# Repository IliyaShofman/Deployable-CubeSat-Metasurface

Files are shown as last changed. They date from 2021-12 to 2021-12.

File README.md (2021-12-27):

## What is this?
This is my research project during my internship at the Reconfigurable Antenna Laboratory in the summer of 2020. I've summarized the 4-month project in the "Supper Report.PDF" file. 

*The goal of this project is to develop a mechanism which would stow and deploy flat, thin Metasurface panels that cover a large area from a small-volume nanosatellite. Novel prototypes, testing setups and measuring methods have been developed and built to validate the design in laboratory settings. This research, sponsored by Thales Alenia Space, will enable the demonstration of technological matureness for deployed meta-surface antenna systems for emerging 5G and IoT space communication applications.*

The SOLIDWORKS model of the concept is sotred in this repository. 

## Design Concept

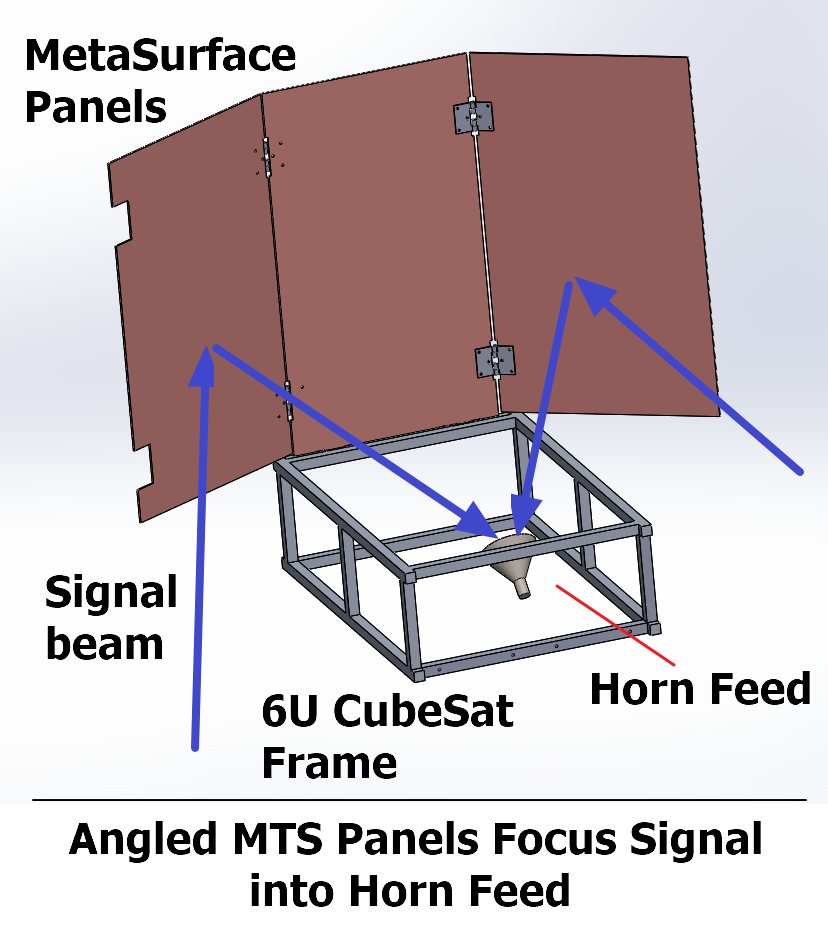
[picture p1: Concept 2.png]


## Deployment Animation

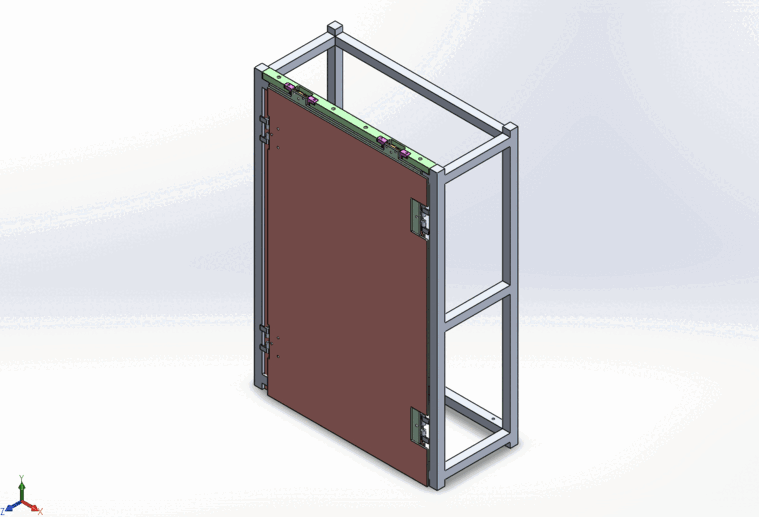
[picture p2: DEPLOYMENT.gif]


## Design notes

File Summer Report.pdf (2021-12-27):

## Deployable Metasurface Antennas for CubeSats

In this report I will summarize the work I have done during the 2020 FYSRF with Dr. Sean V. Hum on Deployable Metasurface Antennas. The goal of this project is to develop a mechanism which would stow and deploy flat, thin Metasurface panels that cover a large area from a small-volume nanosatellite. Novel prototypes, testing setups and measuring methods have been developed and built to validate the design in laboratory settings. This research, sponsored by Thales Alenia Space, will enable the demonstration of technological matureness for deployed meta-surface antenna systems for emerging 5G and IoT space communication applications.

This report will present my contributions to the research project in chronological order, organized by month. At the end, I will reflect on key lessons I learned during the work term.

### May – Understanding the Problem and Conceptual Design:

After being introduced to the research problem, I was encouraged to research deployable space structures in the research literature, which covers a wide range of topics from origami-deploying antennas to inflatable space station modules. Although we had limited input from the stakeholder, we anticipated that a CubeSat-sized satellite would be most appropriate for their mission requirements. Therefore, I focused on learning about CubeSats and deployable solar panel systems. This allowed me to explore functionally similar reference designs and understand the physical constraints on the desired solution.

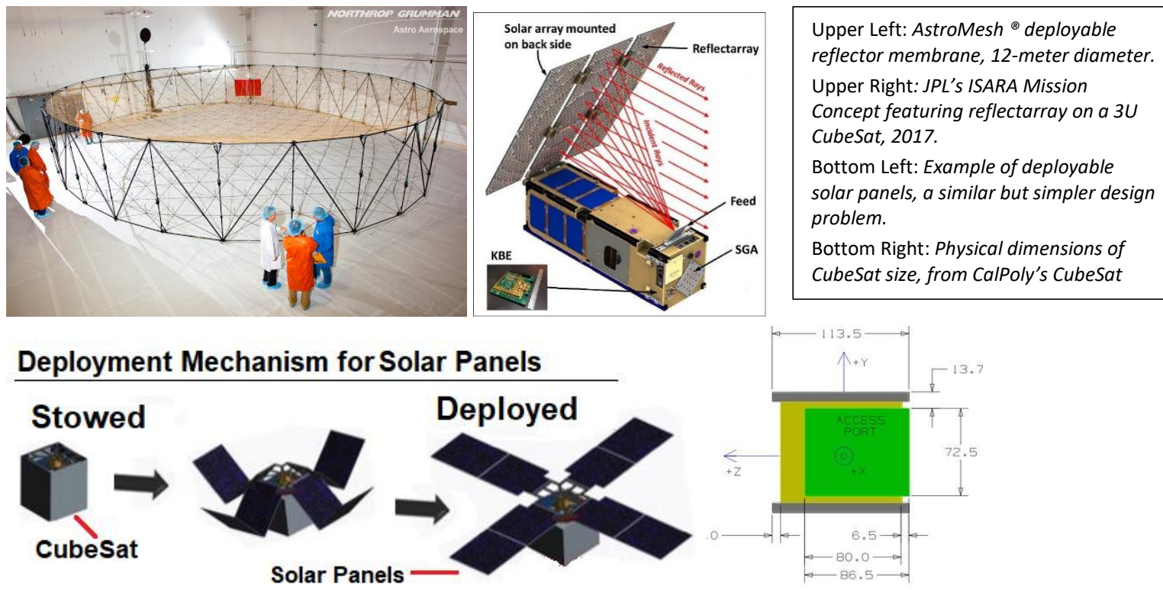
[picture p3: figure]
Upper Left: AstroMesh ® deployable reflector membrane, 12-meter diameter. Upper Right: JPL’s ISARA Mission Concept featuring reflectarray on a 3U CubeSat, 2017. Bottom Left: Example of deployable; problem. Bottom Right: Physical dimensions of CubeSat size, from CalPoly’s CubeSat

At this stage, I began to brainstorm various designs and mechanisms to accomplish the following objectives:

- Stow the deployable Metasurface panels within the space constraints of a 6U CubeSat.
- Reliably release the Metasurface panels upon command.
- Physically move panels into operational configuration, without failure and risk to the satellite.
- Accurately lock the panels in their final positions that provide the best gain and bandwidth.

solar panels, a similar but simpler design

The design of a deployable space system is challenging because a wealth of precautions against must be taken to ensure the design will not fail in space. The concerns over cold-welding, thermal cycling, vacuum out-gassing, and solar radiation are reflected in deliberate design and material choices that differentiate the solution from, say, a kitchen cabinet. To simplify the design, we decided to create a design that can be mounted externally to a 6U CubeSat. While this significantly limits design freedom, we thought it was strategically better to demonstrate Metasurface on a simple, failproof deployment system before testing complex designs.

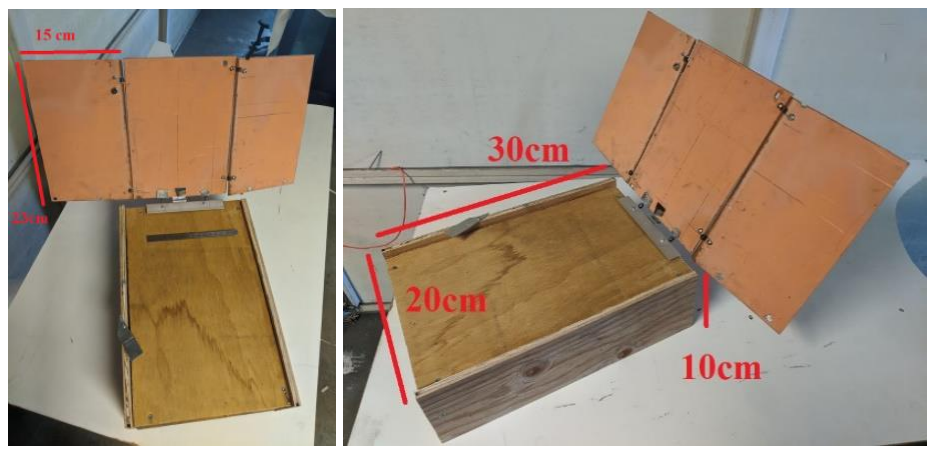
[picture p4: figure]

### June – Initial Prototyping:

After making a conceptual model (pictured above) of the deployment system, I investigated alternatives to individual elements and built basic physical prototypes for each. Options like micro-motors, flexure and SMA joints were eliminated due to higher design complexity; A combination of magnetic clips and blocking plate was chosen for their simplicity; and the Nichrome wire- fishing line solution was chosen for its success in previous space missions.

Hold and Release | Guided Deployment | Final Blocking
Mechanical Latch/ Hook Solenoid and/or electromagnet Nichrome Burn Wire and Fishing Line | Torsional Springs & Hinges Flexure joints Shape Memory Alloy joints Micro-Motors | Spring-loaded Latch Simple block-plate Magnetic Clip Tensioning Cables

Having finalized the conceptual design, I modeled the system in SolidWorks and designed mechanical parts that comprise the system. Custom-built hinges that conform to space constraints and house the torsional springs were designed, along with their mechanical interface with a standard 6U CubeSat frame. The four picture below show the deployment sequence, while the 6 pictures below show detailed closeups of critical design elements.

Conceptual Prototype: 3 panels (folded together) rotate away from the larger face of the 6U CubeSat. Then, two side panels rotate 180 degrees from the middle panel, powered by torsional springs. Alternatives to torsional springs were investigated in June.

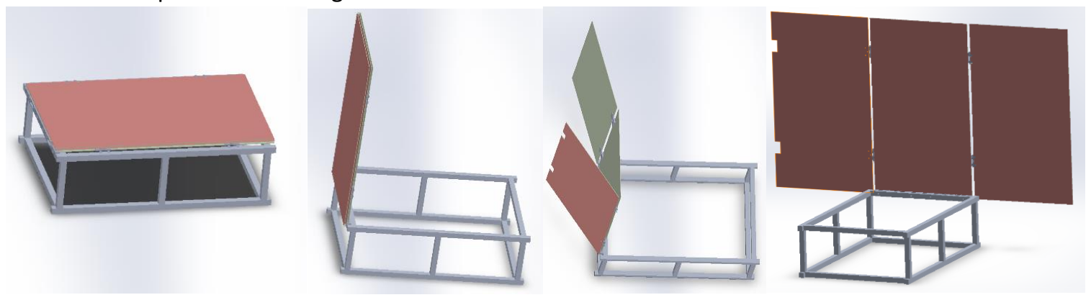
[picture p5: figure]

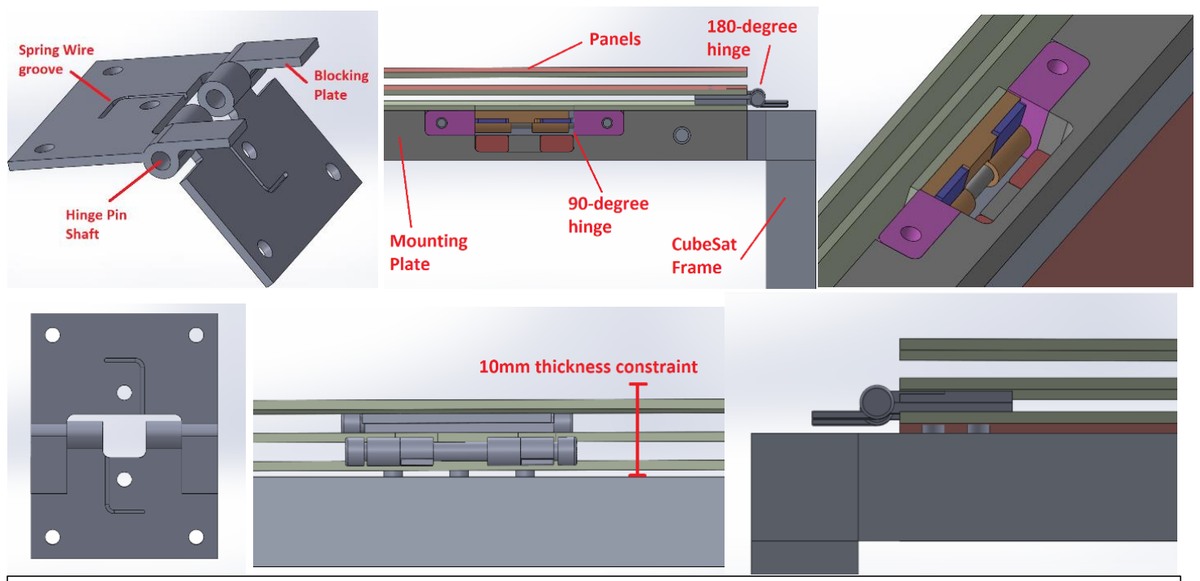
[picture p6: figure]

At this level of design, the primary concerns consisted of dimensions and tolerances for each feature such as a hole, material thickness, length, etc. After ensuring that the parts were realistically sized with an additional safety margin, I contacted several CNC fabrication shops for quotations on part manufacturing costs.

### June - Design of Testing Setup:

Meanwhile, thought was given on how to test the deployment mechanism in a laboratory before launching it into space. It is critical to know if and how the panels may fail to unfold, which may include friction in the joints, manufacturing defects, and material failures. As an extension, the electromagnetic characteristics of the Metasurface may be measured for consistency and accuracy to ensure the antenna will function as expected in space.

To test the deployment mechanism, it is necessary to emulate the space environment – especially microgravity. When the panels deploy on earth, the springs must be made strong enough to fight against gravity forces during the unfolding process. In space, however, these springs will be too strong and could fling the panels too rapidly, which will make the satellite tumble out of control. Thus, a setup that allows for closer-to-realistic mechanical performance testing of the prototype is necessary.

A large cage out of PVC tubing and connectors was devised. Constant force springs and nylon fishing line cables will be used to suspend the CubeSat frame and the deployable panels, thereby bearing the gravitational forces on the prototype. As the panel deploys, low-friction rails will guide the movement of the suspension cables to avoid extraneous tension forces on the prototype. Clearances in the frame can be made to allow electromagnetic measurements to be made without scattering.

Top Left: 3D View of 180-degree hinge. Note that blocking plate prevents hinge from opening more than 180°. Bottom Left: top view of 180-degree hinge.
Top Middle: Side view panels mounting onto CubeSat frame. Top Right: 3D view of 90-degree hinge. Bottom Middle: Thickness view of panels, 8mm out of 10 utilized. Bottom Right: side view of 180-degree hinge fitting in between panels.

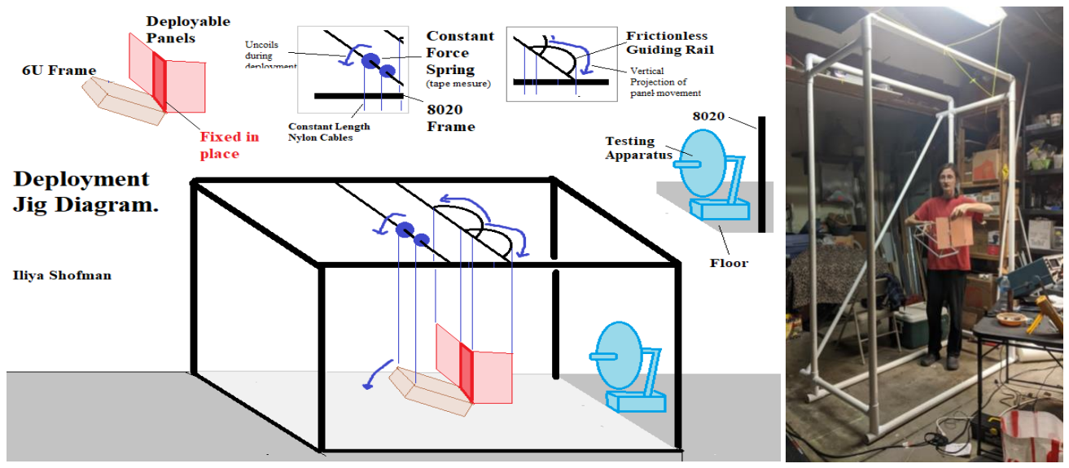
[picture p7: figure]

### July – Presenting Early Concepts:

In the first half of this month, I prepared for a presentation of the conceptual design to the project sponsor, Thales Alenia Space. Their representatives were interested in increasing bandwidth and suggested having the side panels angled towards the feed. This requirement added another element of complexity and uniqueness that differentiates this design from deployable solar panels.

Later in the month, I worked on writing an abstract summarizing my work for the Undergraduate Engineering Research (UnERD) Day Conference at U of T.

### July – Designing Measurement Methods:

While planning a testing procedure in the “cancelled gravity” platform, we concluded that it was necessary to somehow measure the position of the Metasurface panels to quantify the effect of positional inaccuracies of the panels on electromagnetic performance. For example, suppose the panels are supposed to lie in one plane, but end up being angled due to an incomplete deployment or distorted due to thermal gradients in orbit. We would like to know if, the antenna gain, bandwidth, focal position, and scattering pattern will change significantly as a result.

Several methods to measure the position of the panels were developed and prototyped. Since physically touching the panels could disturb their position, we had to consider contactless photogrammetric methods. The table below summarizes and compares these methods, which include a Commercial 3D scanner, a home-made Structured Light Scanner, the Camera Picture Method and the Mirror Method. For the near future, we decided to proceed with the Mirror method since it is the simplest and most impactful measurement on positional inaccuracy.

Left: Diagram showing the deployment testing process. Originally, the frame was planned to be built from 8020 Aluminum. Right: Assembled PVC frame of the testing setup, with author holding CubeSat model for scale.

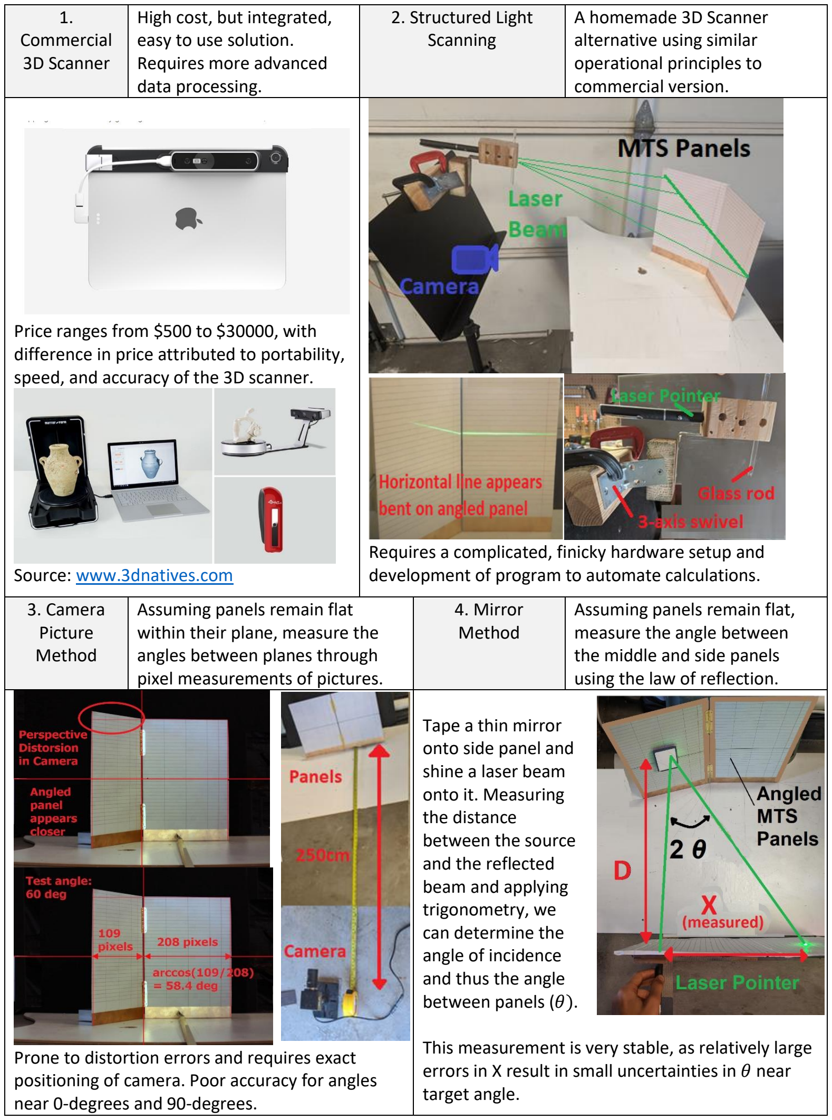
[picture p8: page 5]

1.
Commercial
3D Scanner

High cost, but integrated, easy to use solution.
Requires more advanced
data processing.
2. Structured Light
Scanning

A homemade 3D Scanner
alternative using similar
operational principles to
commercial version.

Price ranges from $500 to $30000, with difference in price attributed to portability, speed, and accuracy of the 3D scanner.

Source: www.3dnatives.com

Requires a complicated, finicky hardware setup and development of program to automate calculations.

3. Camera
Picture
Method

Assuming panels remain flat within their plane, measure the angles between planes through pixel measurements of pictures.

4. Mirror
Method

Assuming panels remain flat, measure the angle between
the middle and side panels using the law of reflection.

Prone to distortion errors and requires exact positioning of camera. Poor accuracy for angles near 0-degrees and 90-degrees.

Tape a thin mirror
onto side panel and
shine a laser beam
onto it. Measuring
the distance
between the source
and the reflected
beam and applying
trigonometry, we
can determine the
angle of incidence
and thus the angle
between panels (θ).

This measurement is very stable, as relatively large errors in X result in small uncertainties in θ near target angle.

### August – Upgrading the Prototype and Improving the Testing Setup:

As requested by Thales, I devised a means to have the panels deploy to an angled position, so that the final angle between panels may be adjusted. This design features a fine-threaded set screw with a spherical tip that can achieve angle positioning with up to 0.2-degree precision. Simplified calculations were made that the ideal angle is about 15°, and that an error of 0.25 degrees will shift the signal focus by 1mm. Since a deviation of up to 1 wavelength (1cm) is tolerable, this translates into a 2.5-degree panel angle accuracy.

A higher fidelity prototype was built to include new design features. It includes a 1:1 scale aluminum frame resembling commercially available models. Small arts-and-crafts hinges were modified to house a torsion spring, thus resembling the custom-designed hinges. A nichrome wire hold-and-release mechanism was designed and successfully implemented.

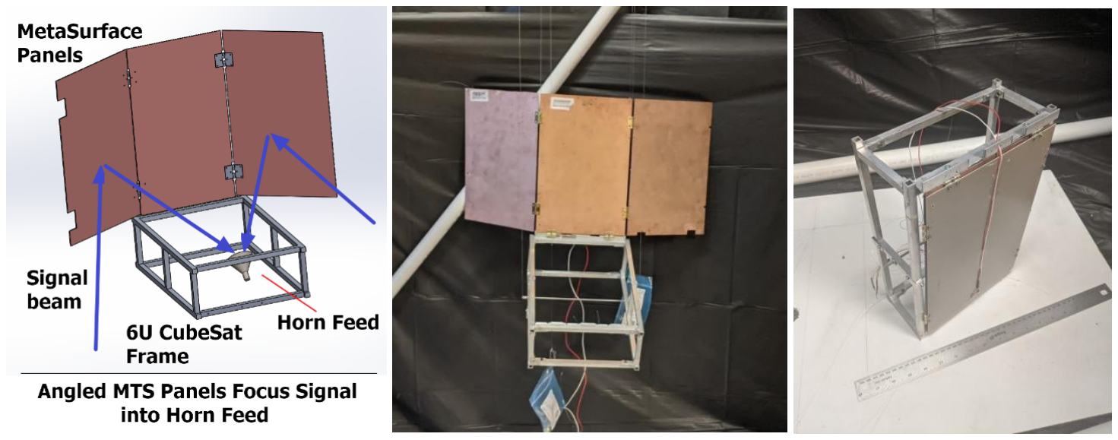
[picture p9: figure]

After preliminary trial runs, several improvements to the testing setup were made. The initial idea of using constant-force springs was scrapped because they had limited travel range and could coil out of control if stretched too far. When the panels were simply suspended from nylon cables and deployed, the satellite jittered and oscillated for several minutes on the suspension system. The designed was changed to suspend all elements using pulleys and counterweights.

After additional tests, it was determined that the sliding rails had some friction, which skewed the deployment of the prototype. It was necessary to make a higher-quality low friction sliding rail that would move smoothly.

After further testing, it was noticed that the side panels bump into suspension cables used to hold the CubeSat frame. Since the CubeSat is suspended by a rod passing through its center of mass, a heavy steel bar was temporarily screwed to the other end to shift the suspension point away from the panels. In the future, the centroid rod must be made sufficiently wide to avoid collision with deploying members.

Left: Metasurface acts as a flat reflector that manipulates EM radiation to focus and amplify signal. Middle: Higher fidelity prototype, deployed configuration.
Right: Stowed configuration fits within 6U CubeSat volume constraints.

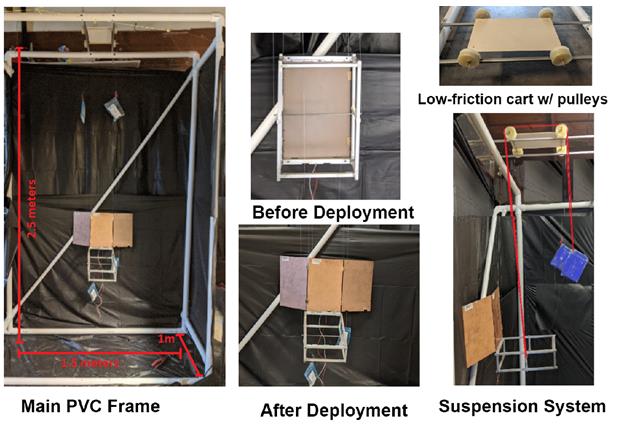
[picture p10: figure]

The picture above shows several views of the testing setup. The table below contains embedded videos of the various failed test runs discussed on the previous page.

Failed Run #1: Pendulum Swinging | Failed Run #2: Heavy Counterbalances + Friction Jamming

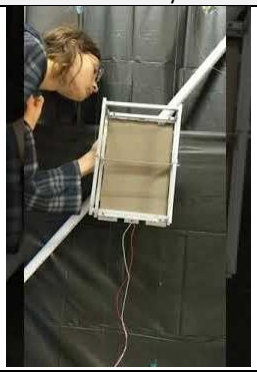
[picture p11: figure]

CubeSat body started swinging like a pendulum because it was simply attached via suspension cable. | Heavy counterbalances and panels jammed against CubeSat frame prevented deployment. Counterweight mass will be adjusted, bigger clearance will be made for rotating parts, and stronger springs will be chosen to overcompensate for deployment failures.

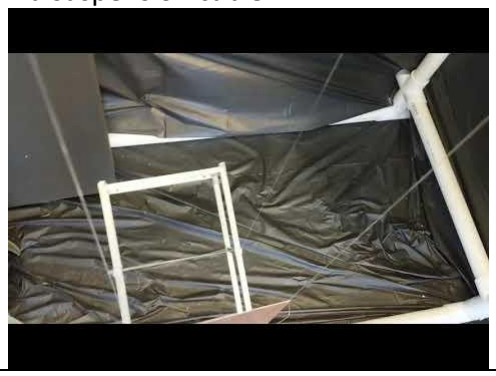
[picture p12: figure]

Since laboratories at U of T remained closed throughout most of the summer, all prototyping work was done in home settings. This prevented a fully functioning testing bed from being assembled and made ready to use at the end of the summer. However, to keep the research moving, a simplified testing setup has been devised which will allow for electromagnetic measurements on the deployed assembly without the CubeSat frame.

The pictures below show this simplified setup. The three unfolding panels are mounted onto a stand which holds the middle panel fixed and vertical. A round mirror is attached to the center of a side panel. Another stand holds the laser pointer for the Mirror Method measurement. Both stands need to be aligned and positioned with respect to each other before measurements.

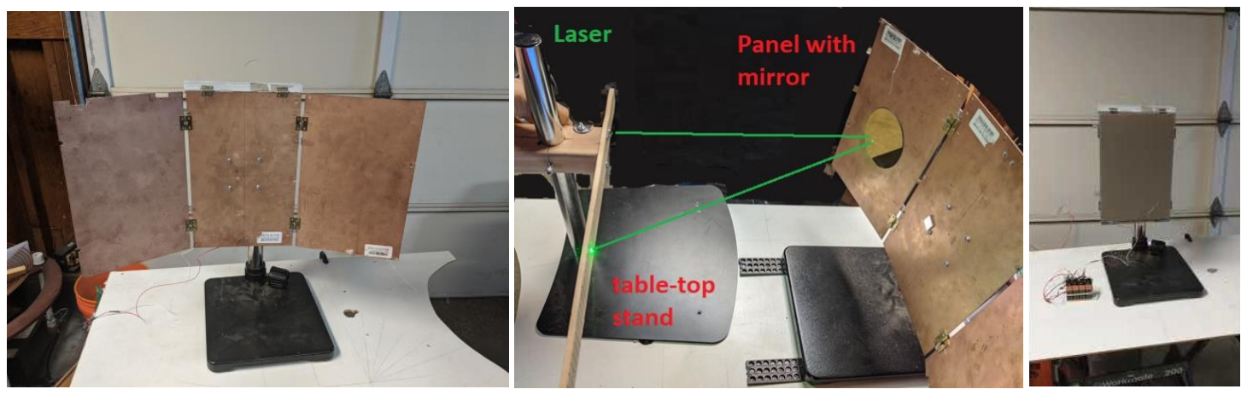
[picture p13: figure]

Left: Deployed panels on stand mount. Middle: Simplified testing setup diagram. Right: Video of simplified deployment test (successful!).

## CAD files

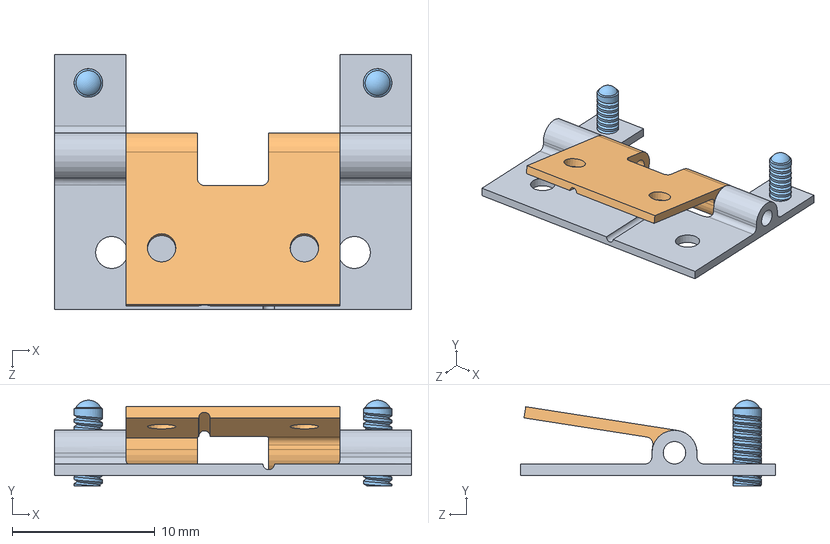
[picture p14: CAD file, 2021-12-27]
SOLIDWORKS_MODEL/180 HInge v2.SLDASM
25.0 x 6.00 x 17.9 mm
180 Hinge Plate Male v3
180 HInge Plate Female v2
Set Screw x 2

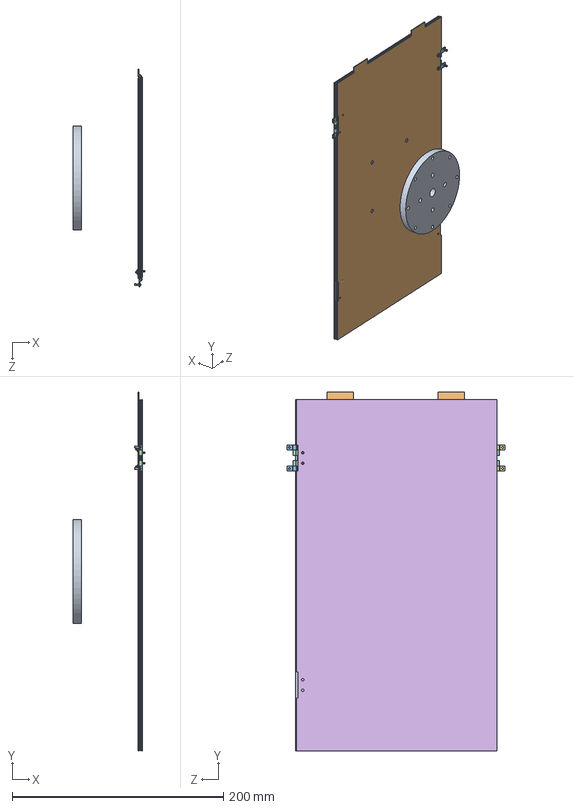
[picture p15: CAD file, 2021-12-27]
SOLIDWORKS_MODEL/Panels and Mount Assembly.SLDASM
67.9 x 340.0 x 206.0 mm
Mounting Plate
Middle Panel
180 Hinge Plate Male
180 Hinge Plate Female
Set Screw x 2
Side Panel
Male
Female
Inner Side Panel
M2 Screw Cone head x 4
M2 Hex Nut Low Profile x 2

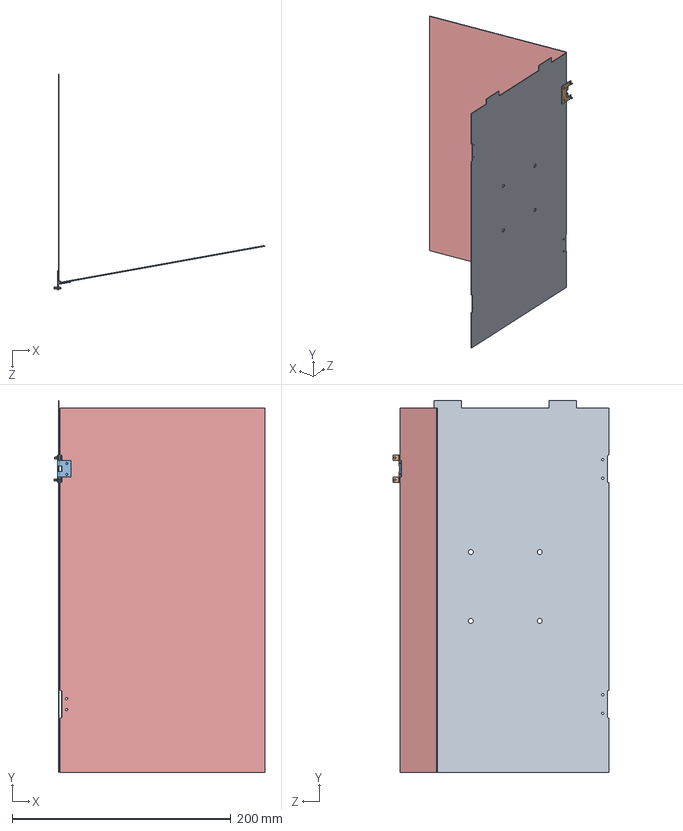
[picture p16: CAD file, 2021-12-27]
SOLIDWORKS_MODEL/180 Panels v1.SLDASM
192.4 x 340.0 x 197.9 mm
Middle Panel
180 Hinge Plate Male v3
180 HInge Plate Female v2
Set Screw x 2
Side Panel

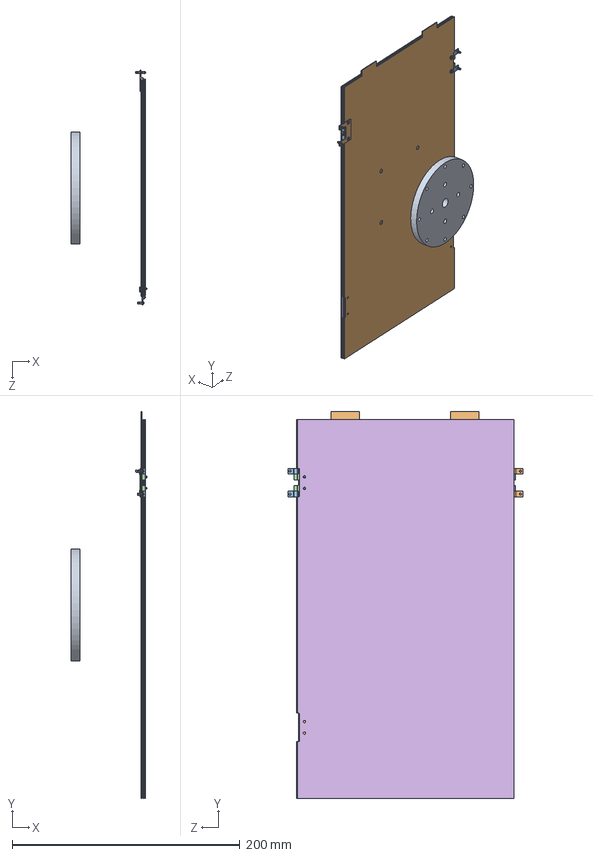
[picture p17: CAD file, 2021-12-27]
SOLIDWORKS_MODEL/Panels and Mount Assembly v2.SLDASM
66.9 x 340.0 x 206.9 mm
Mounting Plate
Middle Panel
Outer Male
Outer Female
Set Screw x 4
Side Panel
Inner Side Panel
M2 Screw Cone head x 6
M2 Hex Nut Low Profile x 4
Inner Hinge M
Inner Hinge F

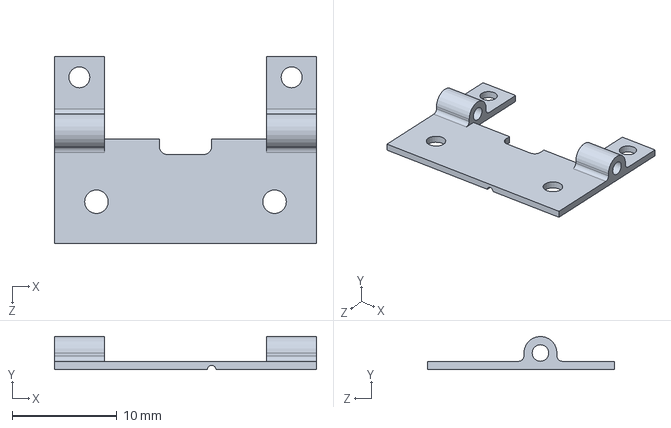
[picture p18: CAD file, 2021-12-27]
SOLIDWORKS_MODEL/180 Hinge Plate.SLDPRT
25.0 x 3.16 x 17.9 mm

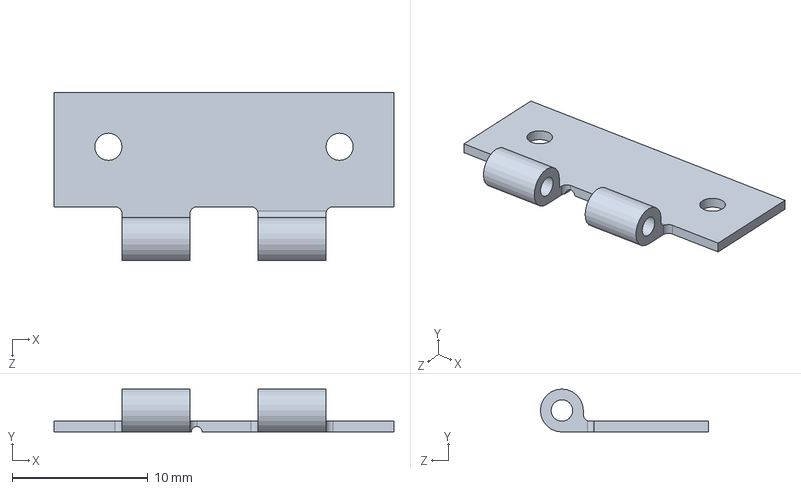
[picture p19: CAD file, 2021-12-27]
SOLIDWORKS_MODEL/180 HInge Plate Female.SLDPRT
25.0 x 3.16 x 12.4 mm

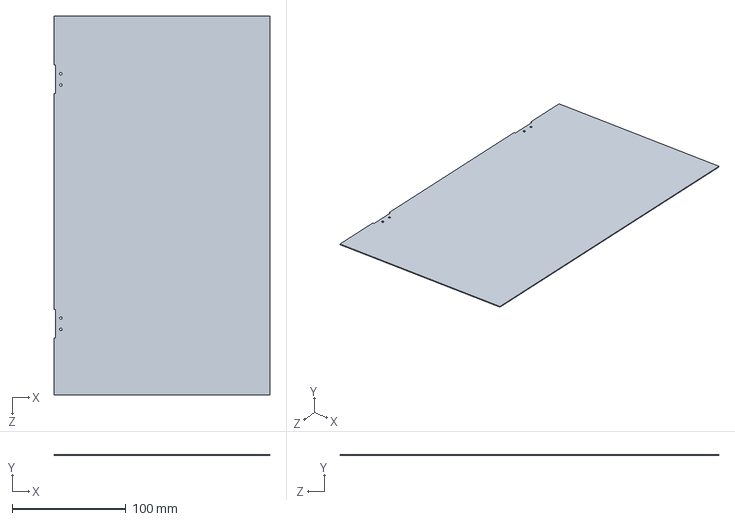
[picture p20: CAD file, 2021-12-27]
SOLIDWORKS_MODEL/Side Panel.SLDPRT
190.0 x 0.79 x 333.0 mm

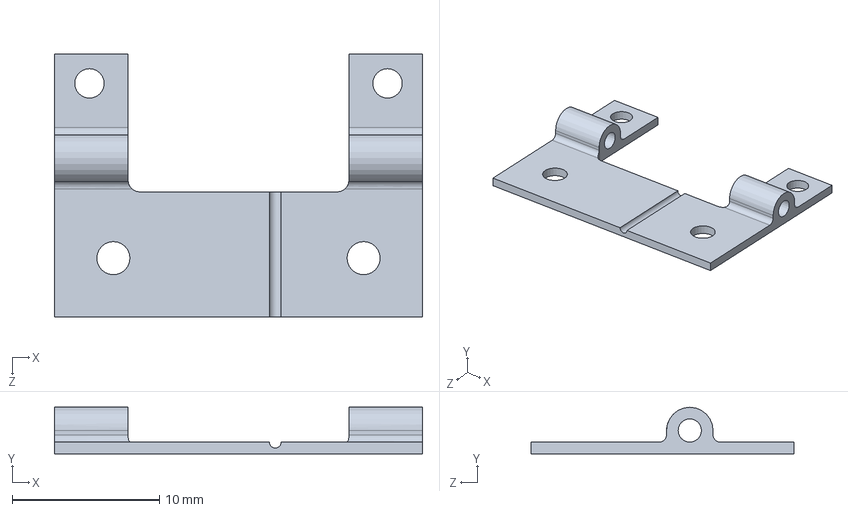
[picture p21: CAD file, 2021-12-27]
SOLIDWORKS_MODEL/180 Hinge Plate Male v3.SLDPRT
25.0 x 3.16 x 17.9 mm

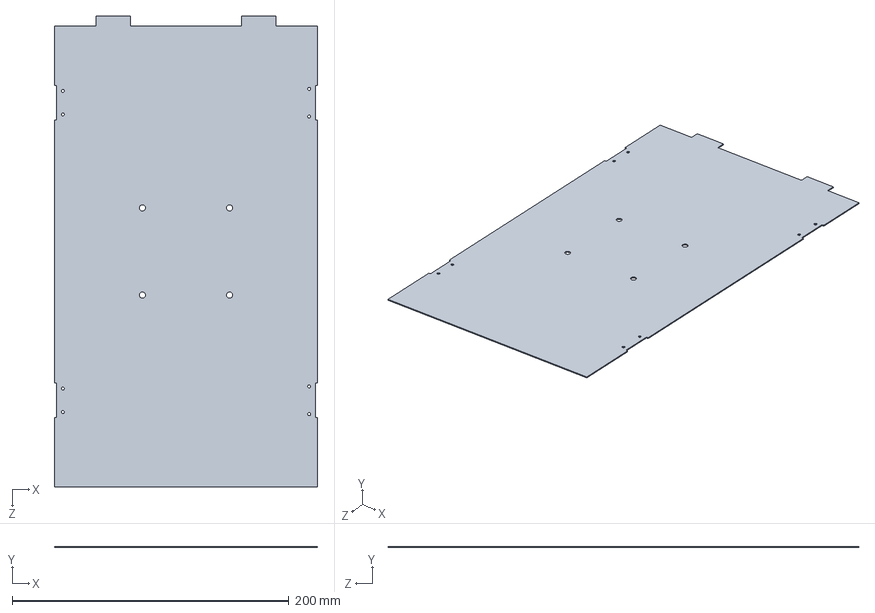
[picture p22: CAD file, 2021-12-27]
SOLIDWORKS_MODEL/Middle Panel.SLDPRT
190.0 x 0.79 x 340.0 mm

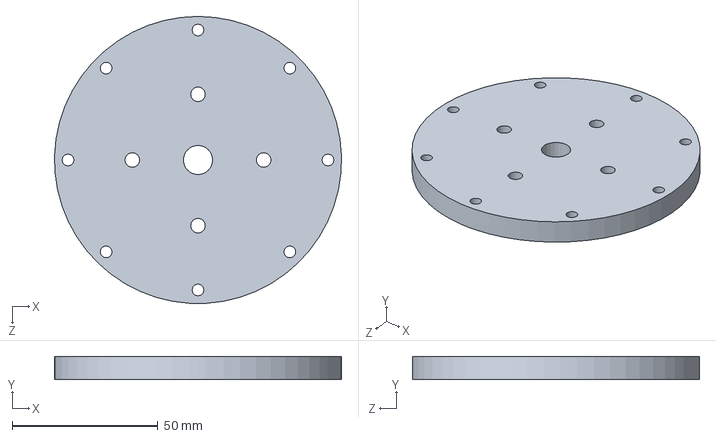
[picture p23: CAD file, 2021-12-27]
SOLIDWORKS_MODEL/Mounting Plate.SLDPRT
98.4 x 8.00 x 98.4 mm

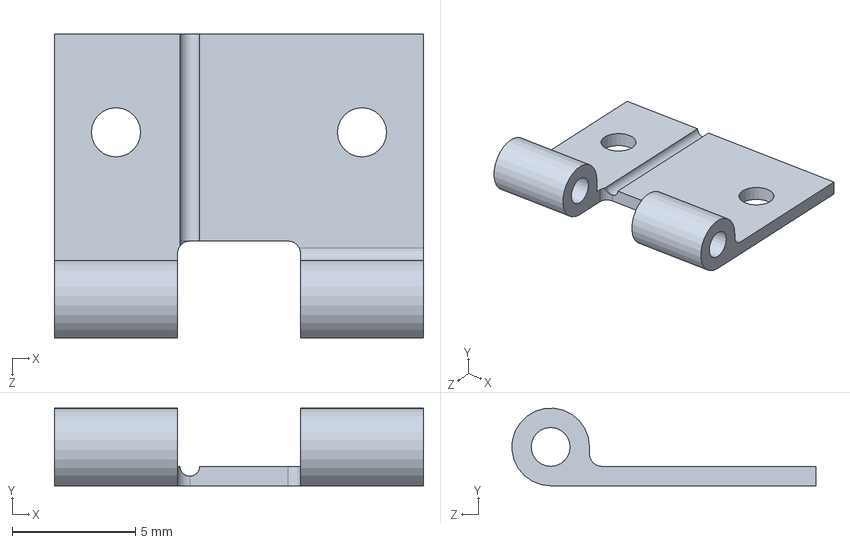
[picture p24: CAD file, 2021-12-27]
SOLIDWORKS_MODEL/180 HInge Plate Female v2.SLDPRT
15.0 x 3.15 x 12.4 mm

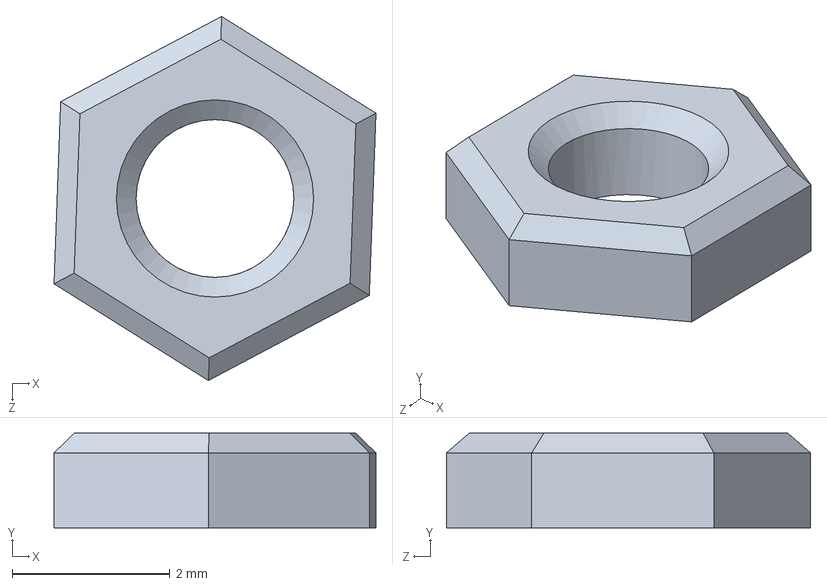
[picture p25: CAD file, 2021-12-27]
SOLIDWORKS_MODEL/M2 Hex Nut Low Profile.SLDPRT
4.08 x 1.20 x 4.62 mm

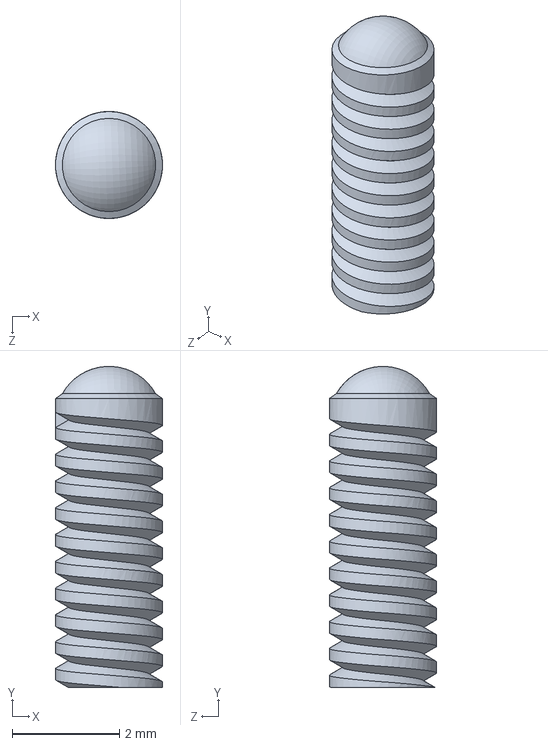
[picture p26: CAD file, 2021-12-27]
SOLIDWORKS_MODEL/Set Screw.SLDPRT
2.00 x 6.00 x 2.00 mm

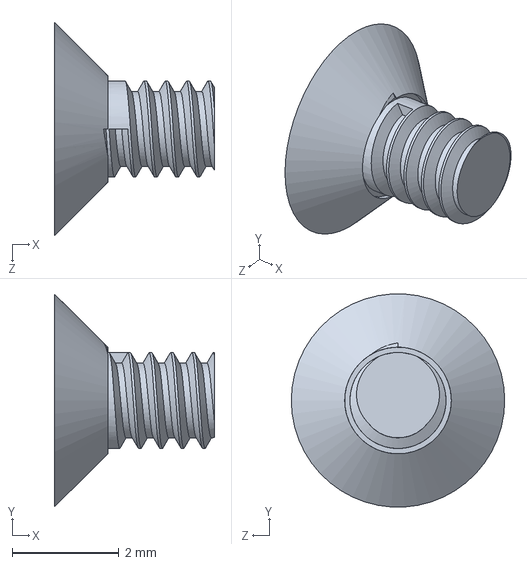
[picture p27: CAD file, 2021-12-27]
SOLIDWORKS_MODEL/M2 Screw Cone head.SLDPRT
3.00 x 3.99 x 4.00 mm

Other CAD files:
SOLIDWORKS_MODEL/Inner Side Panel.SLDPRT
SOLIDWORKS_MODEL/180 HInge v1.SLDASM
SOLIDWORKS_MODEL/Mounting Platre Drawing.SLDDRW
